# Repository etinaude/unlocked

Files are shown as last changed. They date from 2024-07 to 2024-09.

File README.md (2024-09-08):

# 🔑 Unlocked 🔑

## Introduction

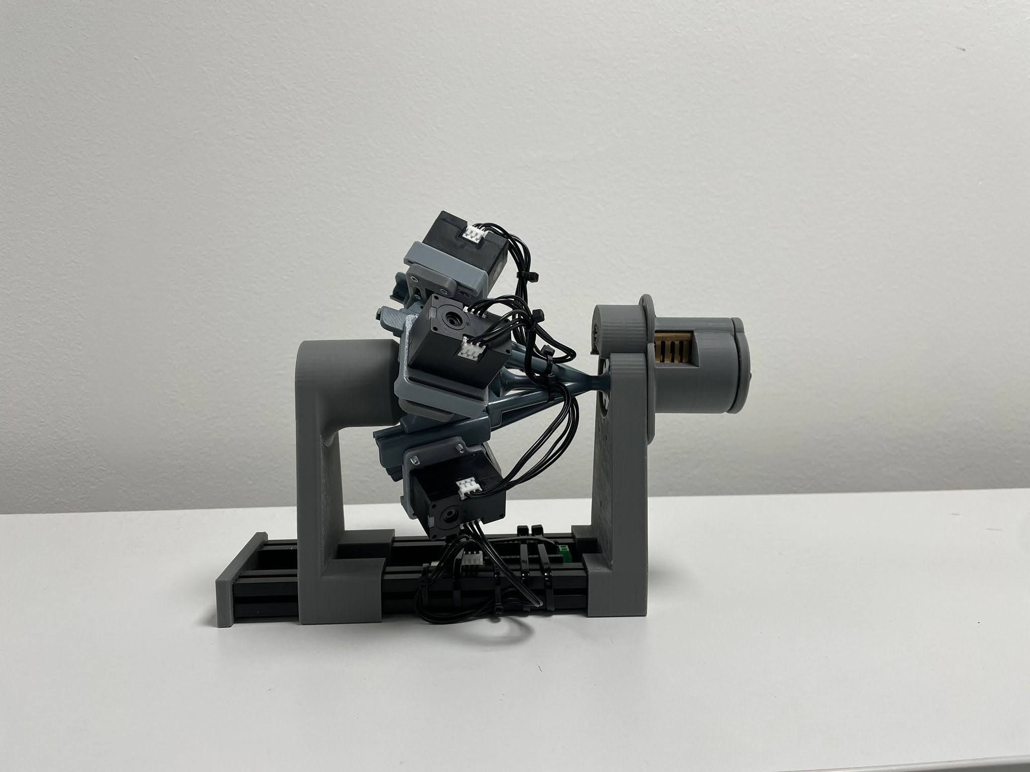
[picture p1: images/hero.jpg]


### Background

An open source Lock picking robot. Basically, there are many skeleton keys in use (the most common example is the TSA 007, [which is bad](https://www.youtube.com/watch?v=GhESSMvf_to)). Having one key which can open MANY different locks, especially without the lock owners people knowing it exists [or can be bought on Aliexpres for a pound](https://www.aliexpress.com/item/1005006407379398.html). It is a massive security issue. However, the TSA, locksmiths etc need to open locks in certain situations, and if you make locks easy to open for them, they are easy to open for everyone.

### 🔒 ➡️ 🔑🤖 ➡️ 🔓

So, lock-picking robot!!! The idea behind this robot is that it will be able to open difficult-to-lick locks. However, it takes a bit of time. That means you can get a lock which this robot would take 5 min to pick, but would require hundreds of keys (rather than a set of 7), and waiting with a very overt device by a lock for 5 min is a lot more obvious than unlocking it with a key which makes it look like you own the lock. 

### How it works

It feeds wire through a hollow key to press each pin and brute force all possible combinations. So security pins do not affect it since it is not looking for force feedback. However, more pins, or potential cut depths (entropy) make it take exponentially longer, it takes about 0.7s per combo so a 4 pin/4 cut depth lock would take about 3 min, but 5 pin/5 cut depth would take about 35 min to try all combos. So it's possible to design a lock with many security pins and an annoying keyway, very hard to pick for a human, but relatively quick for this robot.

### TLDR:

For lock sports/locksmiths its a fun toy, and for everyone else an interesting alternative to skeleton keys (and stop using TSA locks)

### Demo



## 💻 Software

### Prerequirements
- Arduino IDE
- Git
- Using [openrb board manager](https://raw.githubusercontent.com/ROBOTIS-GIT/OpenRB-150/master/package_openrb_index.json)
- Arduino SAMD Board Manager
- DYNAMIXEL2Arduino Library

Follow [this guide](https://emanual.robotis.com/docs/en/parts/controller/openrb-150/#development-environment) to get everything set up

The Source Code is in the repo, fully open source, if you make any changes (please do!) keep them open source as well (GPL 3.0 licence)

## ⚡ Electronics

### Components

- Servo Motors - [Dynamixel xl330-m288-t](https://emanual.robotis.com/docs/en/dxl/x/xl330-m288/) 
- Driver Board - [openrb-150](https://emanual.robotis.com/docs/en/parts/controller/openrb-150/)

## ⚙️ Mechanics

Unlocked uses FDM, SLA and DMLS parts for different levels of precision and strength, it uses 0.4mm copper wire to press the pins. More details in the `/3D files` Folder

### Tools Required

- FDM 3D printer
- Vat Polymerization 3D printer (DLP/SLA)
- (Ideally) DMLS 3D printer
- General Hand tools

## 📝 Notes

A new key blank will be needed for a different kind of lock based on the number of pins and the keyway, the current one can be modified to fit this, this should be made out of DMLS steel, companies like JLCPCB can print this, or you can use a SLA part which will likely break a few times so you'll a few spare.

### Future developments

- Include a more robust way to test if the lock is unlocked (for now it tilts slightly from gravity) but a current feedback servo would be better
- Use current feedback to create a set of possible sets or false sets to reduce the number of combos to try
- Before brute force try combing first

## 📄 References

- [Original 1991 Mechanical Patent -  US patent 5,172,578](https://www.researchgate.net/figure/S-A-Bitzioss-1991-design-for-a-Sputnik-decoder-pick-for-pin-tumbler-locks-US_fig9_271020041)
- [A good YouTube video of a design also based on the 1991 patent](https://www.youtube.com/watch?v=QE9MT1LG-PU)
- [Physical lock decoder](https://www.youtube.com/watch?v=CLcOZhq2GjQ)

## 💬 Contact Me

[https://etinaude.dev/contact](https://etinaude.dev/contact)

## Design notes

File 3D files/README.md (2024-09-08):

# 🔑 Unlocked 🔑 Mechanical

## Files

Everything was designed in Fusion 360

All the files needed are here. The STEP was too big to upload to Git Hub without being zipped and the f3z is massive so if you use Fusion360 and want that DM me. Otherwise, you can use the STEP, 3MF or STLs

### Print Settings

FDM - Doesn't matter too much, these parts have loose tolerances, 0.12mm layer height is recommended \
DLP - As small a layer height as possible, as little support as possible, it should be designed to not need much support \
DMLS - Either printed vertically or horizontally, as fine detail as possible. 

## BOM

All costs in GBP as of Sept 2024 \
The total cost is about £200

### Electronics

| Part | Model | Count | Cost per unit | Total Cost | URL |
| --- | --- | ----- | --- | --- | --- |
| Servo Motor | xl330-m288 | 5 | 26.30 | 131.5 | https://emanual.robotis.com/docs/en/dxl/x/xl330-m288/ |
| Motor controller | openrb-150 | 1 | 28.30 | 28.30 | https://emanual.robotis.com/docs/en/parts/controller/openrb-150/ |
| USB cable | USB C data cable | 1 | 2 | 2 | NA |

### Mechanical

Always have lots of spare wire and screws

| Part | Notes | Count |
| --- | --- | ----- |
| Wire | 0.4 mm copper wire | 100 |
| Aluminium extrusion | 2020 profile | 1 |
| m3x8 countersunk screw  | | 29 |
| m2x10 countersunk screw | | 65 |
| m3x60 screw | | 1 |

### 3D Printed Parts

FDM for bigger parts
DLP (resin) parts are used for low-friction and high-precision
DMLS (Metal powder bed) for strong parts (JLCPCB can print this for you)

| Part | Material | Count | Notes |
| --- | --- | ----- | --- |
| hub | DLP | 1 | |
| internal gear | FDM | 1 | |
| key | DMLS | 1 | Make spare if using DLP |
| | | | |
| **Motor modules** | | 5 | Parts below are per module |
| rail | DLP | 1 | |
| carriage | DLP | 1 | |
| motor mount | FDM | 1 | |
| linkage | FDM | 1 | |
| circle | FDM | 1 | |
| | | | |
| **lock Holder** | FDM | 1 | Parts below are per module |
| lock holder | FDM | 1 | |
| end cap | FDM | 1 | |
| | | | |
| **Mech Holder** | FDM | 1 | Parts below are per module |
| base | FDM | 1 | |
| end cap | FDM | 1 | |
| top | FDM | 1 | |
| | | | |

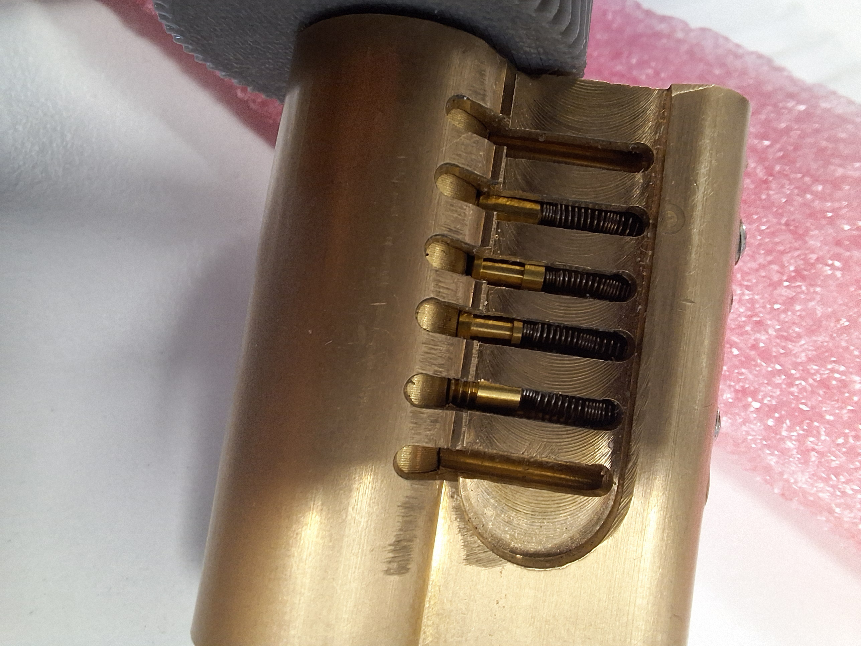
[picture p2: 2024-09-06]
images/barrel.jpg

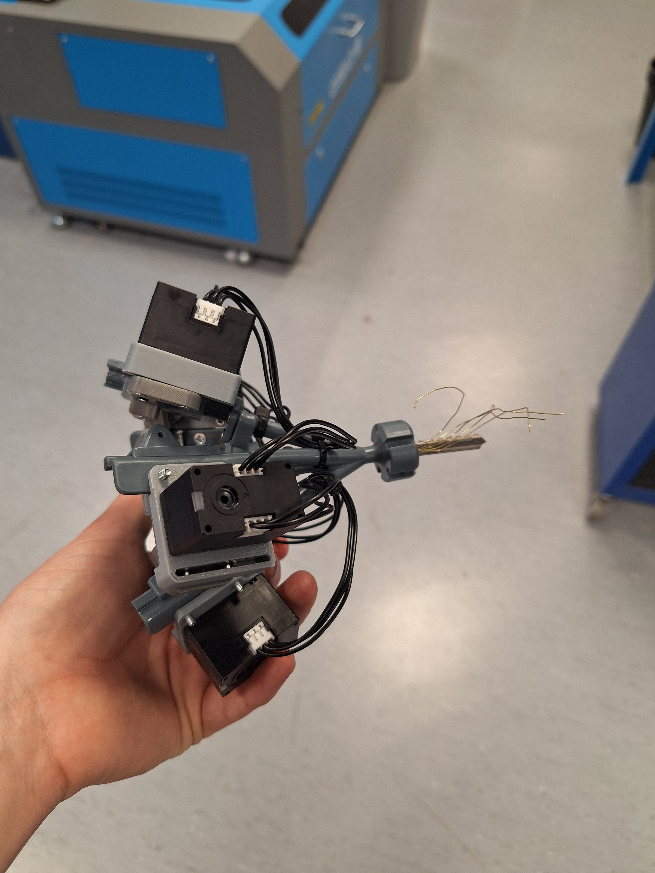
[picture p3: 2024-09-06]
images/bot alone.jpg

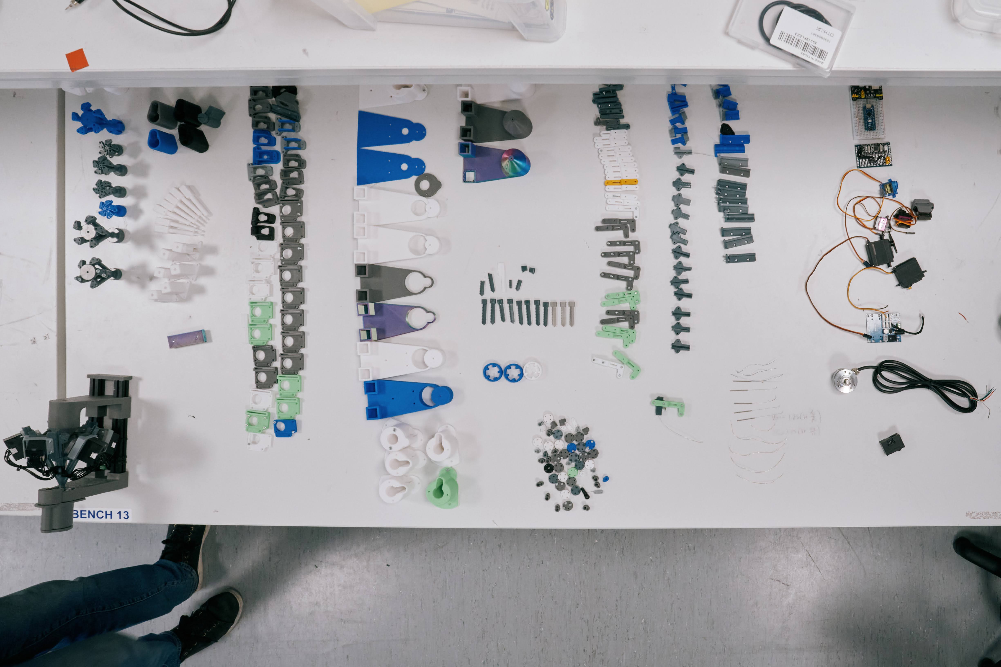
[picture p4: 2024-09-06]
images/prototypes.jpg

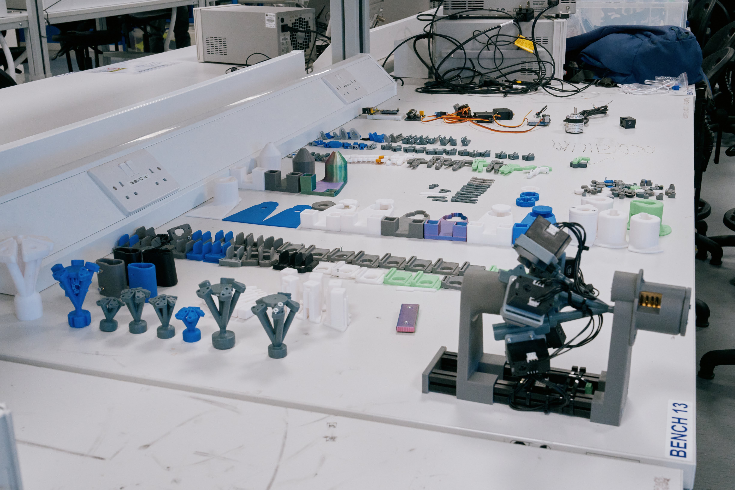
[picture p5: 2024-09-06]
images/prototypes2.jpg

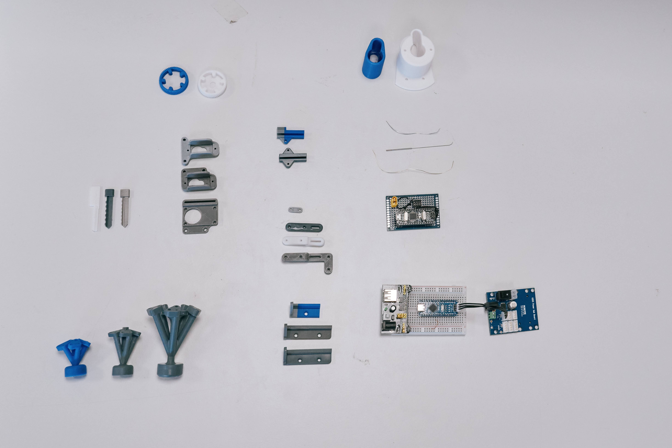
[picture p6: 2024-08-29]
images/major prototypes.jpg

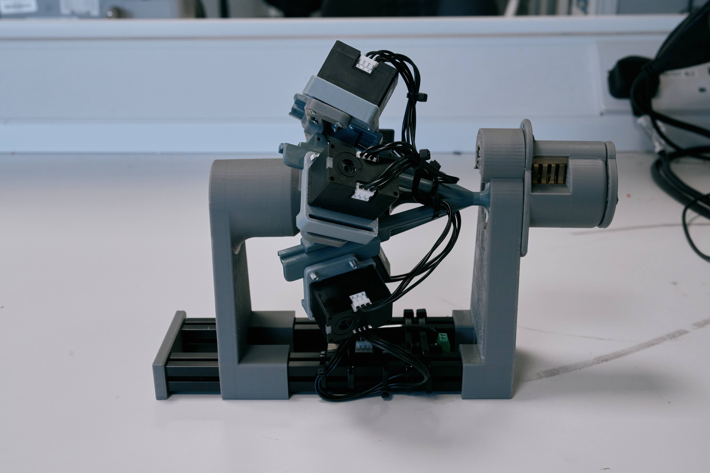
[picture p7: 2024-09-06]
images/full.jpg

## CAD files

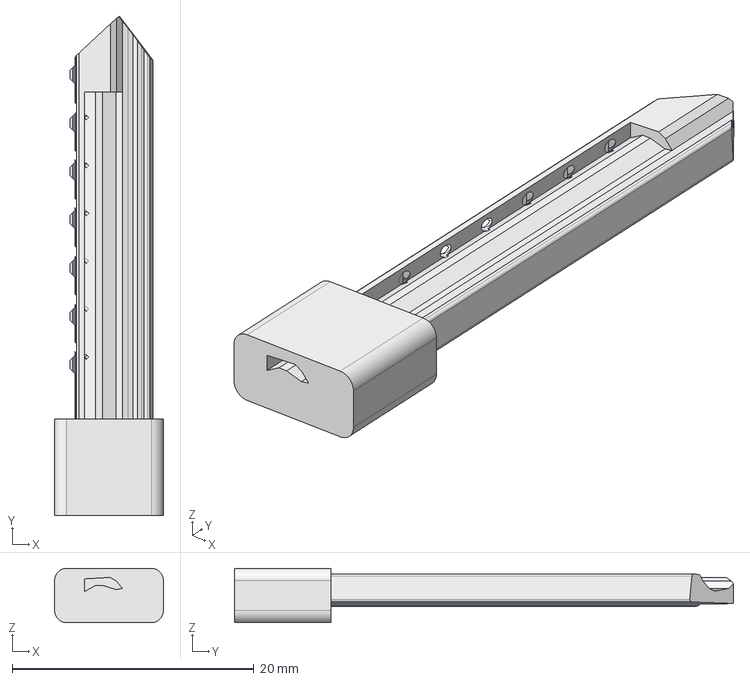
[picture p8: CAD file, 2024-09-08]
3D files/Key/key v14.step
9.00 x 41.3 x 4.50 mm

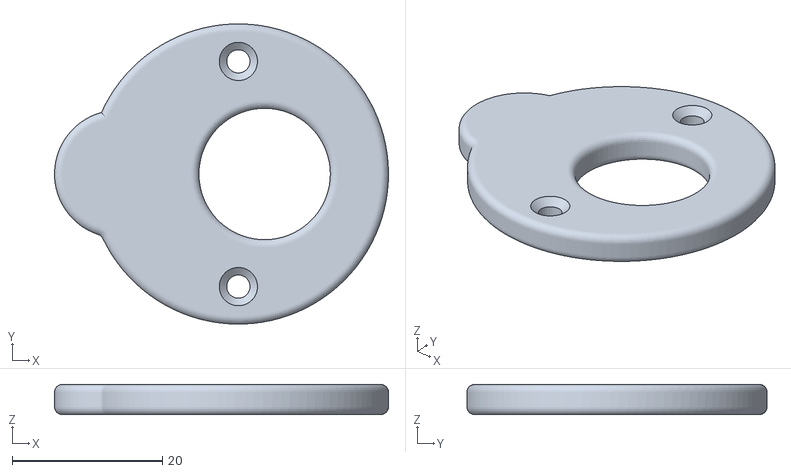
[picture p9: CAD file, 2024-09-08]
3D files/STLs/Lock Holder/end cap.stl
44.5 x 40.0 x 4.00

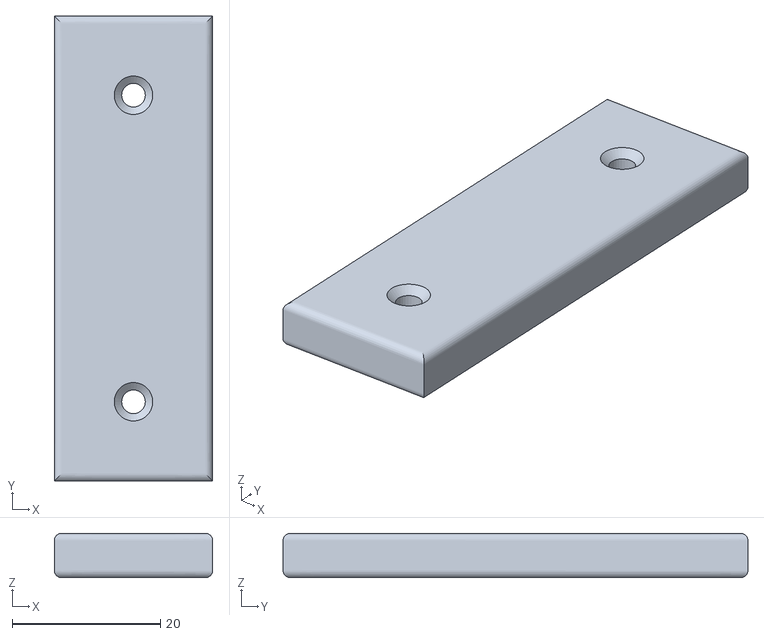
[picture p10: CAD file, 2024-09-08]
3D files/STLs/Mech Holder/end cap.stl
21.4 x 62.8 x 6.00

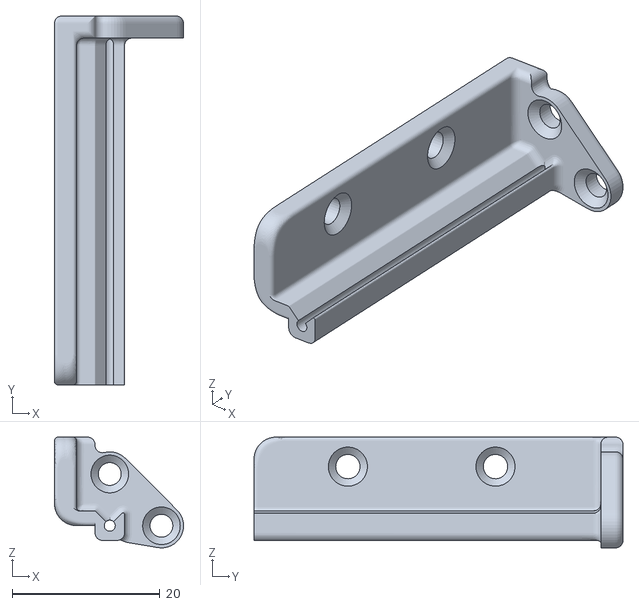
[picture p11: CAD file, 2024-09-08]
3D files/STLs/Motor Modules/Rail.stl
17.5 x 50.0 x 15.0

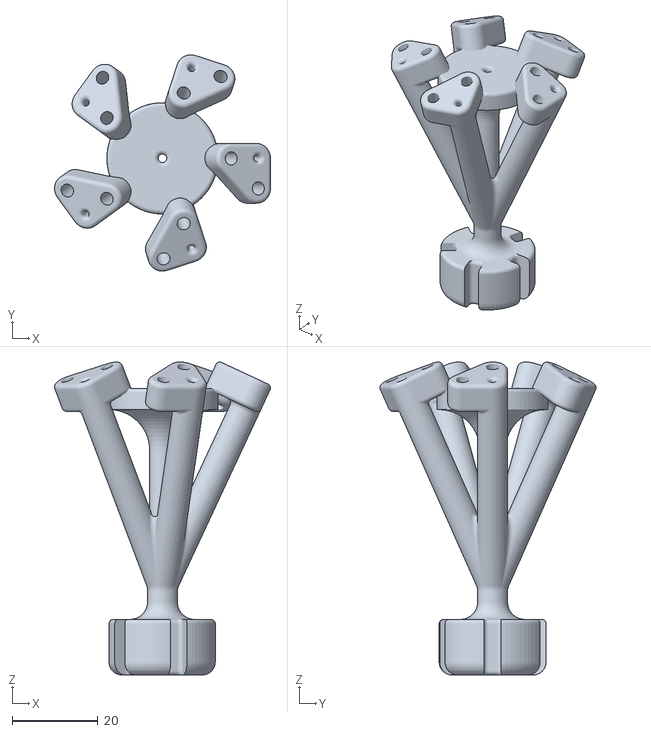
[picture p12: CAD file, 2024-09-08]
3D files/STLs/hub.stl
50.5 x 50.5 x 73.1

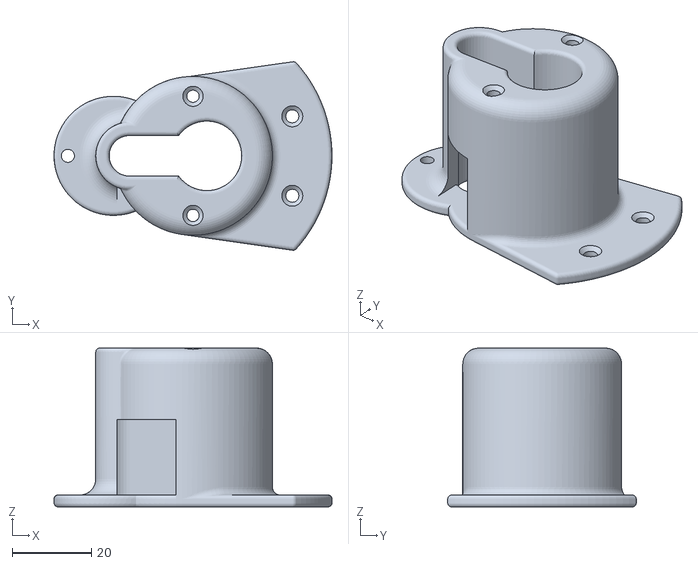
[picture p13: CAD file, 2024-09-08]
3D files/STLs/Lock Holder/lock holder.stl
70.0 x 47.5 x 40.0

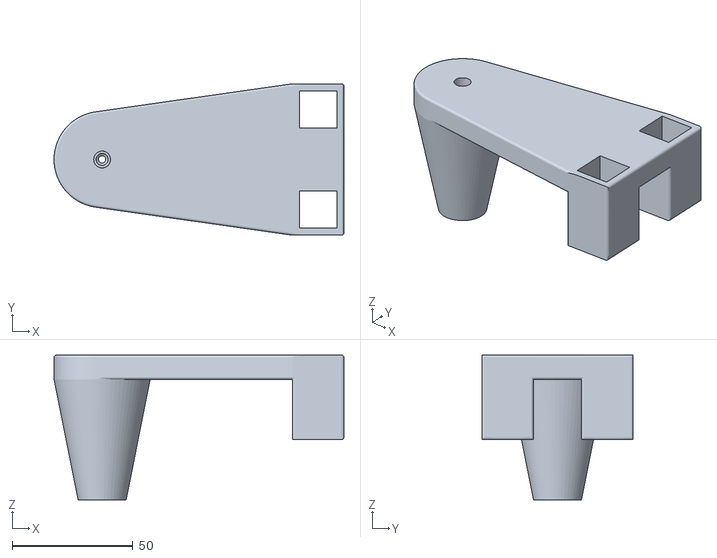
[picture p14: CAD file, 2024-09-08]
3D files/STLs/Mech Holder/top.stl
120.2 x 62.8 x 60.0

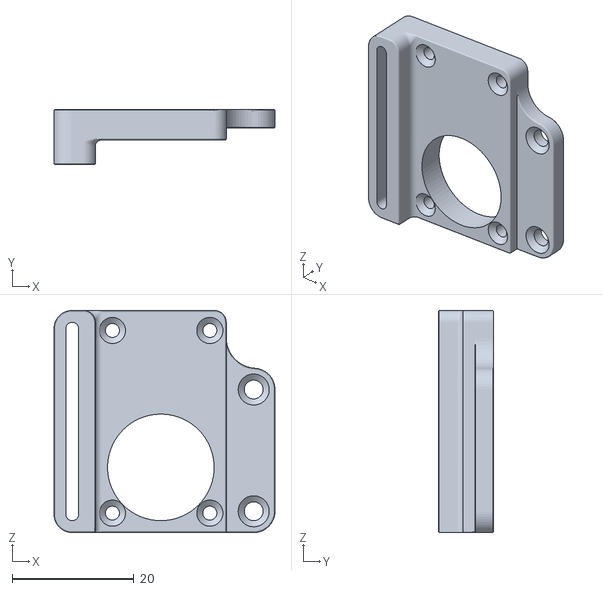
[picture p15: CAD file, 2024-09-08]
3D files/STLs/Motor Modules/motor mount.stl
36.3 x 9.00 x 36.5

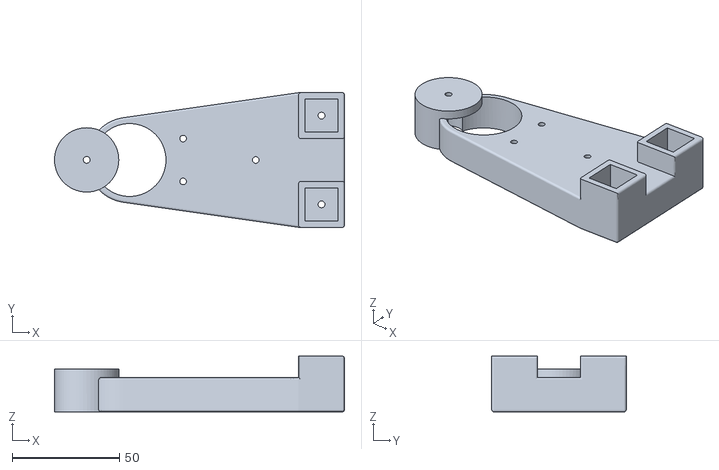
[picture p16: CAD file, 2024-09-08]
3D files/STLs/Mech Holder/base.stl
135.3 x 62.8 x 26.0

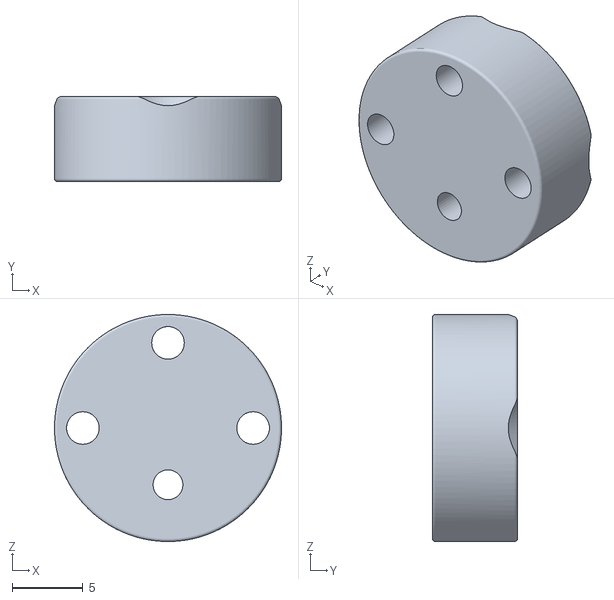
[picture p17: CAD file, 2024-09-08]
3D files/STLs/Motor Modules/circle.stl
16.0 x 6.00 x 16.0

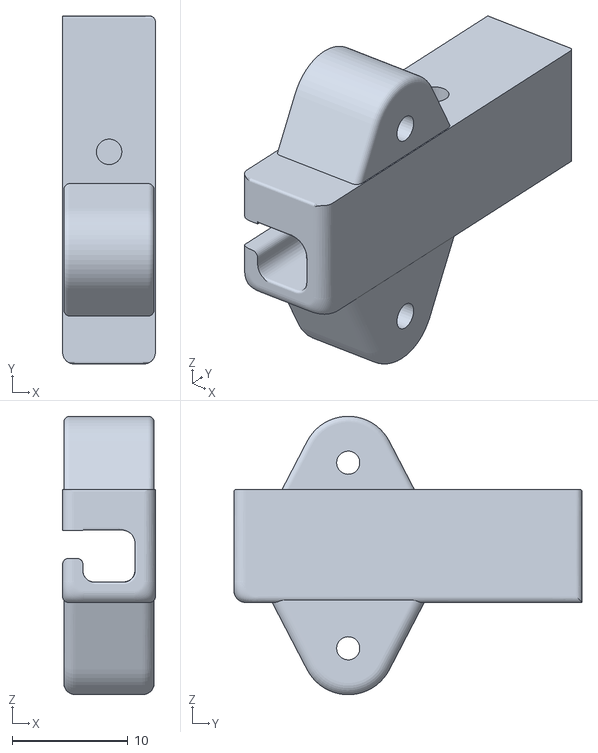
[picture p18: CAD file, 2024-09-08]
3D files/STLs/Motor Modules/carriage.stl
8.00 x 30.0 x 24.0

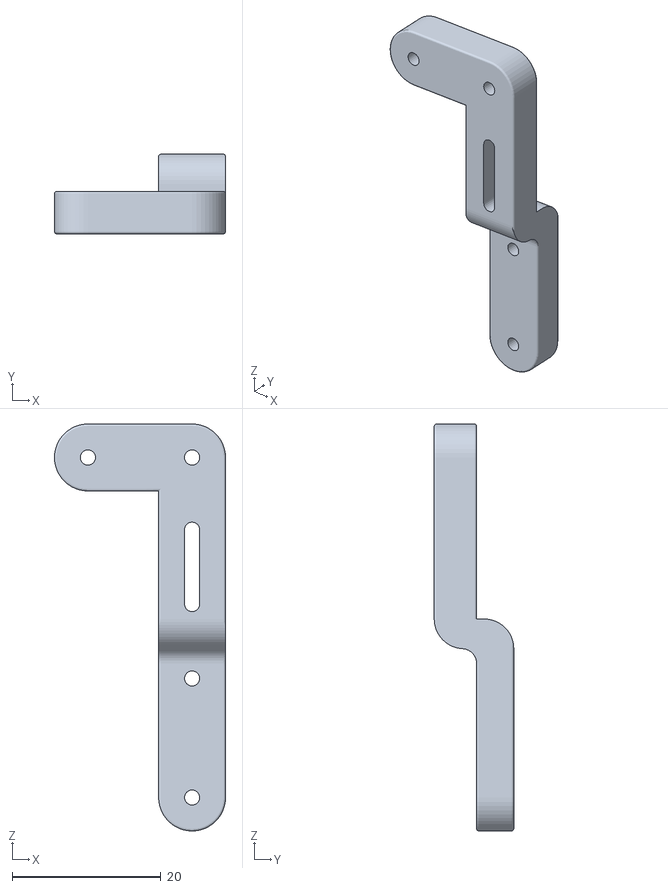
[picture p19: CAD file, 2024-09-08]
3D files/STLs/Motor Modules/Linkage.stl
23.0 x 10.7 x 54.7

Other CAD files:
3D files/STLs/key.stl
3D files/Key/Key.f3d
3D files/Key/key v14.3mf

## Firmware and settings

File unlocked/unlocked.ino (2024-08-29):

#include "pin.h"

bool isLocked = true;
Pin pins[PIN_STACKS] = { Pin(1, 0) ,Pin(2, 135), Pin(3, 0), Pin(4, 0), Pin(5, 0) };

void setup() {
  Serial.begin(115200);
  for (int i = 0; i < PIN_STACKS; i++) {
    pins[i].init();
  }
  Serial.println("Ready");
  Serial.println("~~~~~~~~~~~~");
}

void loop() {
  // serialDebug();
  // bruteForce();
  wearIn();
  // resetAll();
}

void swingTest() {
  pins[0].goToAngle(0);
  Serial.println("0");
  delay(1000);

  pins[0].goToAngle(90);
  Serial.println("90");
  delay(1000);
}


void serialDebug() {
  if (!Serial.available()) return;

  String input = Serial.readString();
  int pin = input.substring(0, 1).toInt();
  int depth = input.substring(2).toInt();

  Serial.print("Pin - ");
  Serial.println(pin);
  Serial.print("Depth - ");
  Serial.println(depth);

  pins[pin].setDepth(depth);

  printState();
  delay(1000);
}

void wearIn(){
  for (int i = PIN_STACKS - 1; i >= 0; i--) {
    pins[i].setDepth(5); 
    pins[i].resetDepth();
  }
}

void resetAll(){
  for (int i = PIN_STACKS - 1; i >= 0; i--) {
    pins[i].resetDepth();
  }
}


void bruteForce() {
  // Increment the least significant digit
  pins[PIN_STACKS - 1].incDepth();

  // Handle carry-over between digits
  for (int i = PIN_STACKS - 1; i >= 0; i--) {
    if (pins[i].depth == CUT_COUNTS) {
      pins[i].resetDepth();
      if (i > 0) {
        pins[i - 1].incDepth();  // Carry-over to the next digit
      }
    } else {
      break;  // No more carry-over needed
    }
  }
 
  printState();
}


void printState() {
  Serial.println("State");

  for (int i = 0; i < PIN_STACKS; i++) {
    Serial.print(i);
    Serial.print(":");
    Serial.print(pins[i].printMotorPos());
    Serial.print(" ");
  }
  Serial.println();
  Serial.println("~~~~~~~~~~~~");
}


void testLock() {
  // try rotate

  // check force/rotation
  int force = 0.2;

  printState();
  if (force > 0.5) {
    Serial.println("Failed to unlock");
  } else {
    Serial.println("Unlocked!!!");
    isLocked = false;
  }
}

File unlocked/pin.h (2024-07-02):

// Please refer to e-Manual(http://emanual.robotis.com/docs/en/parts/interface/dynamixel_shield/) for available range of value.
#include "env.h"
#include <Dynamixel2Arduino.h>

#define DXL_SERIAL Serial1

Dynamixel2Arduino dxl(DXL_SERIAL);

using namespace ControlTableItem;

class Pin {
public:
  int DXL_ID;
  int depth;
  float current_pos = 0;
  float offsetAngle = 0;

  Pin(int ID, float offset) {
    DXL_ID = ID;
    depth = 0;
    offsetAngle = offset;
  }

  Pin(int ID) {
    Pin(ID, 0);
  }


  void init() {
    setupMotors();
    resetDepth();
  }

  void setupMotors() {
    dxl.begin(115200);
    dxl.setPortProtocolVersion(DXL_PROTOCOL_VERSION);
    dxl.ping(DXL_ID);  // Get DYNAMIXEL information

    // Turn off torque when configuring items in EEPROM area
    dxl.torqueOff(DXL_ID);
    dxl.setOperatingMode(DXL_ID, OP_POSITION);
    dxl.torqueOn(DXL_ID);

    // Limit the maximum velocity in Position Control Mode. Use 0 for Max speed
    dxl.writeControlTableItem(PROFILE_VELOCITY, DXL_ID, SPEED);
  }

  void setDepth(int depthIn) {
    depth = depthIn;
    moveServo();
  }

  void incDepth() {
    depth++;
    moveServo();
  }

  void resetDepth() {
    depth = 0;
    moveServo();
  }

  void goToAngle(float angle) {
    dxl.setGoalPosition(DXL_ID, angle, UNIT_DEGREE);
    delay(600);
    current_pos = dxl.getPresentPosition(DXL_ID, UNIT_DEGREE);
  }

  void moveServo() {
    float pos = baseAngles[depth] + offsetAngle;

    goToAngle(pos);
  }

  float printMotorPos() {
    current_pos = dxl.getPresentPosition(DXL_ID, UNIT_DEGREE);
    return current_pos;
  }
};

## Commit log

2024-06-03 inital arduino
2024-06-24 moved files for arduino IDE
2024-09-03 [ImgBot] Optimize images
    *Total -- 19,716.04kb -> 18,194.59kb (7.72%)
    /images/bot alone.jpg -- 3,220.08kb -> 2,896.23kb (10.06%)
    /images/motors.jpg -- 3,215.56kb -> 2,899.96kb (9.81%)
    /images/assembled blade.jpg -- 1,433.58kb -> 1,307.24kb (8.81%)
    /images/wires.jpg -- 3,437.33kb -> 3,135.40kb (8.78%)
    /images/key blades.jpg -- 4,438.06kb -> 4,097.36kb (7.68%)
    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
2024-09-08 Added 3D models and BOM
    [Key.f3d, Linkage.stl, Rail.stl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]
